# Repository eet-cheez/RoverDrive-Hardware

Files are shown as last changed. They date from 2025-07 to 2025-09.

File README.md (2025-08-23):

# RoverDrive-Hardware
A custom PCB for a robot powered by an esp32 microcontroller that has pins to control 4 servos plus one for sub-micro servo at 3.3v (in case it burns out at 5v). It also can support multiple other devices like LEDs or sensors and has an IMU to know its direction.





### Why am I doing this?
Last year, I built a robot that was controlled by connecting to an app. The problem is that the inside was a mess of wires and modules floating around, so it was a pain to fix and improve. I decided a PCB could fit more features while also being much easier to assemble and access.

## Details
- The microcontroller is an ESP32-S3-mini-1. I only really chose it because it seemed compact, but there are probably much better options. 
- For the IMU, it uses a BNO055, which does all of the calculations internally to find its orientation. Might be a bit overkill, but I want to make sure it works properly.
- The board uses a basic ams1117-3.3 to to power all of the 3.3v devices.
- Power is supplied to the board via a 1s lipo battery, which gets boosted to 5v by a mt3608 regulator.
- PCB designed in KiCad.
### Schematic: 

### PCB: 


#### CAD:
This is that the robot looks like with a model of the PCB (in TinkerCad):
 


The robot chassis needed to be changed to fit the PCB. Files have been attached if needed.

## BOM
| Item | Description | Quantity | Cost |
|---|---|---|---|
|ESP32-S3-MINI-1-N8|	the microcontroller	|1	|$6.15 |
|NFM18PC104R1E3D|	100nf capacitor	|13	|$1.69|
|PTS647SN50SMTR2 LFS|	reset and boot buttons|	2	|$0.46|
|GRM188C81A226ME01D|	22uf ceramic capacitor|	3	|$0.87|
|TAJA226K010RNJ|	22uf tantalum capacitor. for ams1117-3.3	|2|$0.70|
|SS34| schottky diode	|1|$0.52|
|SRP7028AA-220M|	22uh inductor	for 5v regulator|1|$1.11|
|C1608X7T1A106M080AC|	10uf ceramic capacitor	|3|	$0.69|
|06031A220FAT2A|	22pf ceramic capacitor for gyro|3	|$1.32|
|CRCW060310K0FKEI|	10k resistor	|7	|$1.05|
|CRCW06035K10FKEC|	5.1k resistor	|3	|$0.36|
|RNCE0603BTE1K00|	1k resistor	|2|$0.42|
|ERJ-3RBD7501V|	7.5k resistor	|2|$0.30|
|ABS07-32.768KHZ-7-T|	32.768 kHz crystal for gyro|1|$0.82|
|BNO055|	9 axis IMU	|1|$12.34|
|USB4105-GF-A	|USB c receptacle, 16 contact|1|$0.78|
|MT3608|	boost converter. used to increase battery voltage to 5v (already have)|	1	|$0|
|AMS1117-3.3|	3.3v voltage regulator	|1	|$0|
|2.54mm pin headers	|for servos	|5| $0|
|Molex picoblade connector|fits with the battery, probably|1|$0|
|JST Connectors (2-pin, 3-pin, 4-pin)|Probably JST XH|3|$0|
|PCB|from JLCPCB|1|$41.71 **(See below for price explanation)***|
**Total:			$71.29**

Sheet with part links: https://docs.google.com/spreadsheets/d/1vR1n98YzZK8dJmbvGAbjTAVUf36cDbNLpNew4ql-z88/edit?usp=sharing

### * PCB Price Explanation
I'm exhibiting the full Roverdrive project at Open Sauce this year and did not have much time to create the hardware (need to finish by the 19th, difficult with Undercity taking up time). In order to get the PCB on time, I had to pay way more for shipping and couldn't spend much time optimizing the cost. I've already bought all of the parts, and I understand if Hack Club doesn't want to reimburse the full cost. If needed, I would gladly take a smaller, more reasonable reimbursement.

### Finished Project




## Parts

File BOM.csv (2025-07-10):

Item | Description | Amount | Total Cost
ESP32-S3-MINI-1-N8 |  | 1 | $6.15
NFM18PC104R1E3D | 100nf capacitor | 13 | $1.69
PTS647SN50SMTR2 LFS | reset and boot buttons | 2 | $0.46
GRM188C81A226ME01D | 22uf ceramic capacitor | 3 | $0.87
TAJA226K010RNJ | 22uf tantalum capacitor. for ams1117-3.3 | 2 | $0.70
SS34 | ss34 schottky diode | 1 | $0.52
SRP7028AA-220M | 22uh inductor | 1 | $1.11
C1608X7T1A106M080AC | 10uf ceramic capacitor | 3 | $0.69
06031A220FAT2A | 22pf ceramic capacitor | 3 | $1.32
CRCW060310K0FKEI | 10k resistor | 7 | $1.05
CRCW06035K10FKEC | 5.1k resistor | 3 | $0.36
RNCE0603BTE1K00 | 1k resistor | 2 | $0.42
ERJ-3RBD7501V | 7.5k resistor | 2 | $0.30
ABS07-32.768KHZ-7-T | 32.768 kHz 3.2 mm x 1.5 mm crystal | 1 | $0.82
BNO055 | 9 axis IMU | 1 | $12.34
USB4105-GF-A | USB c receptacle, 16 contact | 1 | $0.78
MT3608 | boost converter. used to increase battery voltage to 5v (already have) | 1 | $0
AMS1117-3.3 | 3.3v voltage regulator (already have) | 1 | $0
2.54mm pin headers | for servos (already have) | 5 | $0
Molex picoblade connector | fits with the battery, probably (already have) | 1 | $0
JST Connectors (2-pin, 3-pin, 4-pin) | No specific type, just any that fit on the board. (already have) | 3 | $0
PCB (x5) + shipping + 1 day | from JLCPCB, see readme for explanation | 1 | $41.71
Total: |  |  | $71.29
Sheet with Links: |  |  | https://docs.google.com/spreadsheets/d/1vR1n98YzZK8dJmbvGAbjTAVUf36cDbNLpNew4ql-z88/edit?usp=sharing

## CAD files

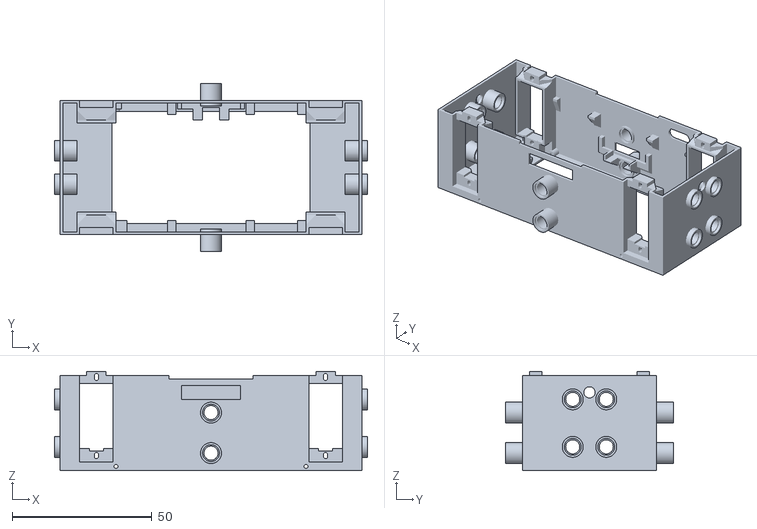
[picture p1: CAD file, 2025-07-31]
CAD/Roverdrive_Chassis.stl
112.0 x 60.0 x 35.5

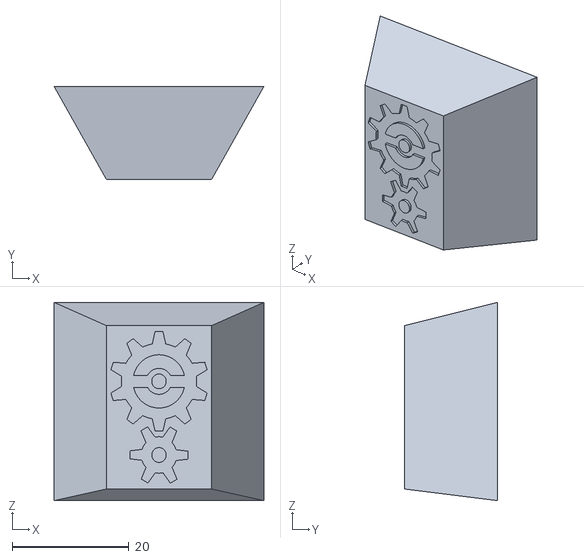
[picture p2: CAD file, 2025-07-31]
CAD/Roverdrive_Side.stl
36.0 x 16.0 x 34.0

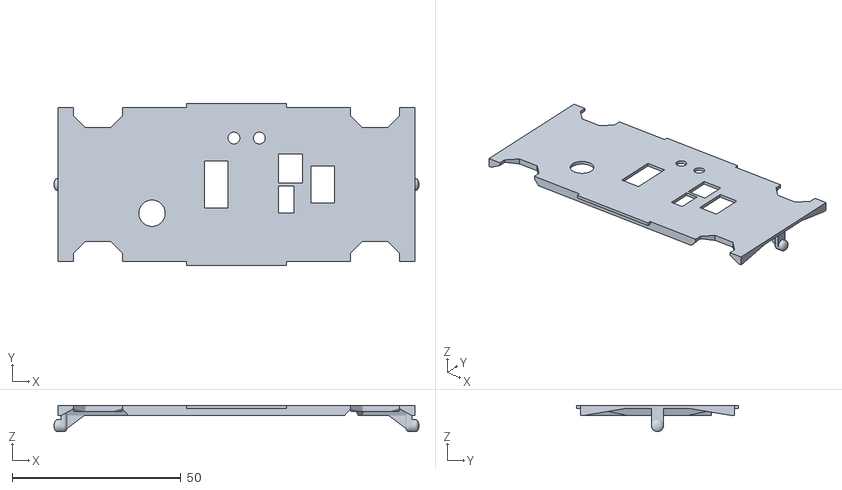
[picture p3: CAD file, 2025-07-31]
CAD/Roverdrive_Lid.stl
108.0 x 48.0 x 7.80

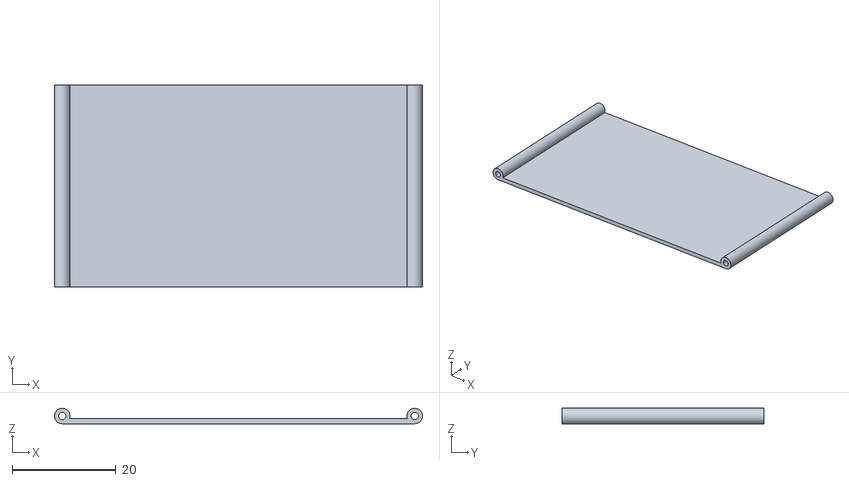
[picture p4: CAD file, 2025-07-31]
CAD/Roverdrive_BottomDoor.stl
71.0 x 39.0 x 3.00

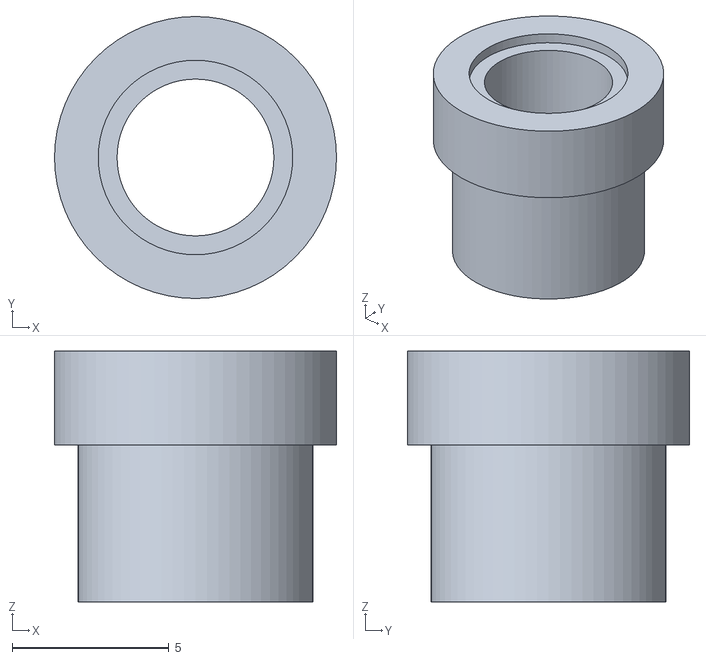
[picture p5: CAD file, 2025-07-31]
CAD/LidHoleConnection.stl
9.00 x 9.00 x 8.00

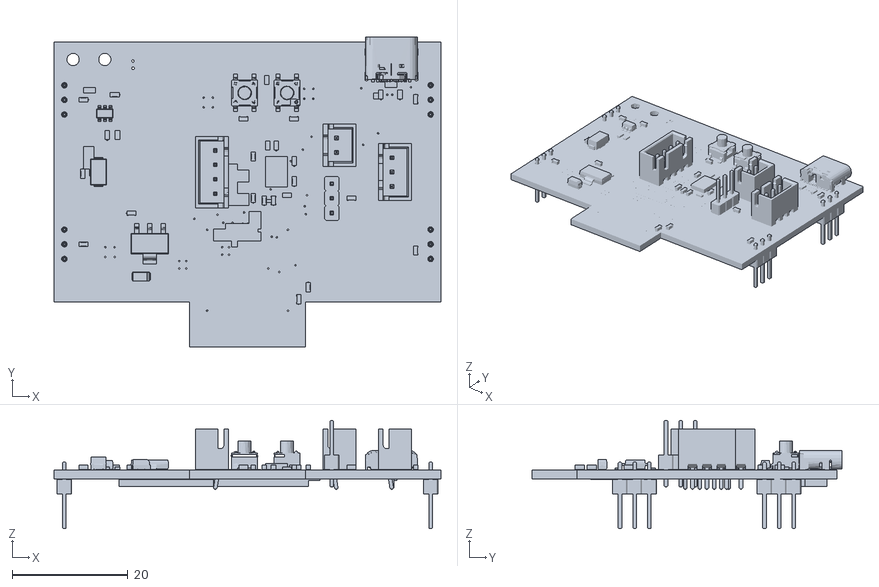
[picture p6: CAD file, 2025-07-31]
CAD/Roverdrive_PCB.stl
67.0 x 53.7 x 18.8

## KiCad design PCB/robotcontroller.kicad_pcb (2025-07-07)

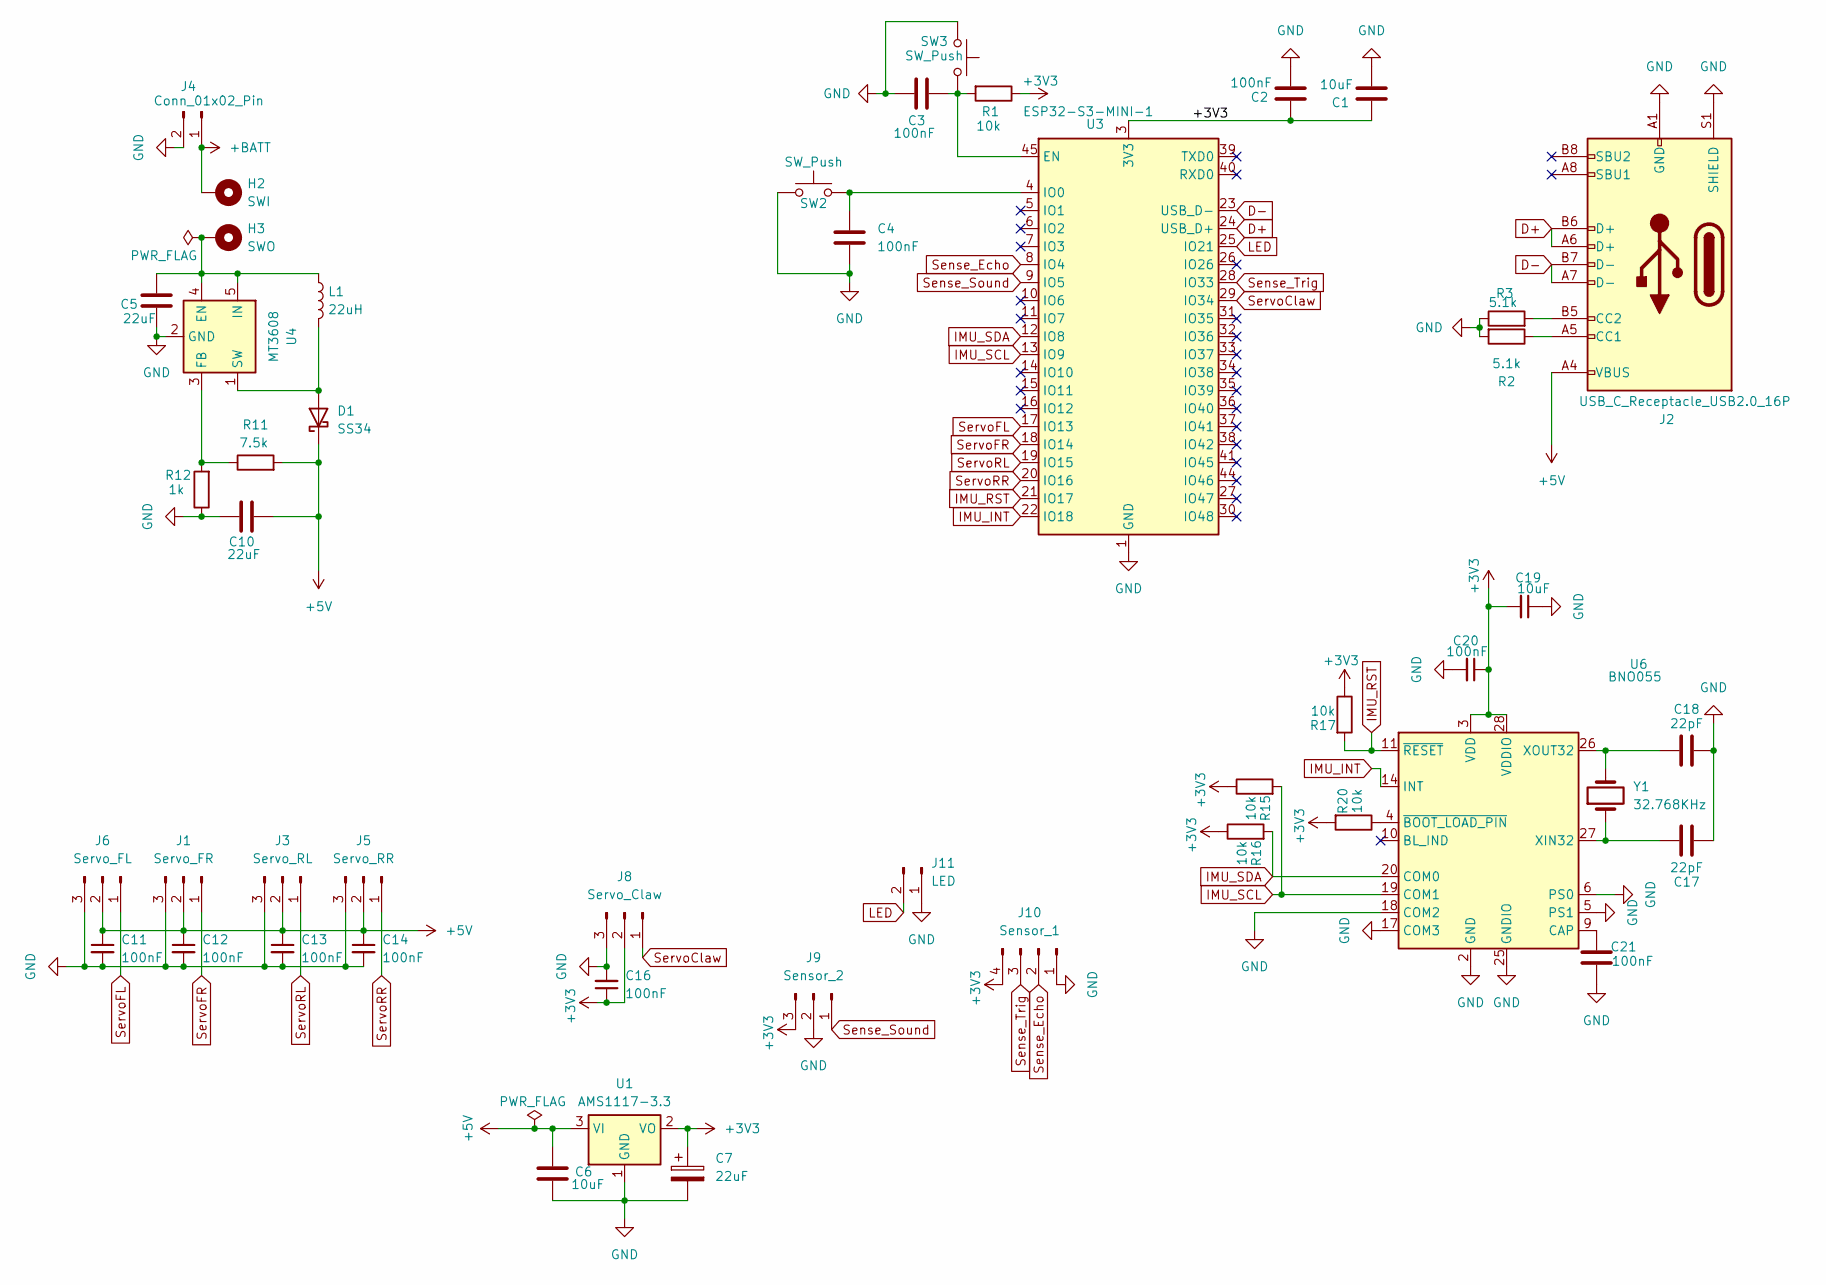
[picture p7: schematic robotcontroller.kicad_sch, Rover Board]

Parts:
C1, C6, C19: 10uF; C_0603_1608Metric
C2, C3, C4, C11, C12, C13, C14, C16, C20, C21: 100nF; C_0603_1608Metric
C5, C10: 22uF; C_0603_1608Metric
C7: 22uF; CP_EIA-3216-18_Kemet-A
C17, C18: 22pF; C_0603_1608Metric
D1: SS34; D_SMA
H2: SWI; SolderWire-1.5sqmm_1x01_D1.7mm_OD3mm
H3: SWO; SolderWire-1.5sqmm_1x01_D1.7mm_OD3mm
J1: Servo_FR; PinHeader_1x03_P2.54mm_Vertical
J2: USB_C_Receptacle_USB2.0_16P; USB_C_Receptacle_GCT_USB4105-xx-A_16P_TopMnt_Horizontal
J3: Servo_RL; PinHeader_1x03_P2.54mm_Vertical
J4: Conn_01x02_Pin; Molex_PicoBlade_53048-0210_1x02_P1.25mm_Horizontal
J5: Servo_RR; PinHeader_1x03_P2.54mm_Vertical
J6: Servo_FL; PinHeader_1x03_P2.54mm_Vertical
J8: Servo_Claw; PinHeader_1x03_P2.54mm_Vertical
J9: Sensor_2; JST_XH_B3B-XH-A_1x03_P2.50mm_Vertical
J10: Sensor_1; JST_XH_B4B-XH-A_1x04_P2.50mm_Vertical
J11: LED; JST_XH_B2B-XH-A_1x02_P2.50mm_Vertical
L1: 22uH; L_Bourns_SRP7028A_7.3x6.6mm
R1, R15, R16, R17, R20: 10k; R_0603_1608Metric
R2, R3: 5.1k; R_0603_1608Metric
R11: 7.5k; R_0603_1608Metric
R12: 1k; R_0603_1608Metric
SW2, SW3: SW_Push; SW_SPST_PTS647_Sx50
U1: AMS1117-3.3; SOT-223-3_TabPin2
U3: ESP32-S3-MINI-1; ESP32-S2-MINI-1
U4: MT3608; SOT-23-6
U6: BNO055; LGA-28_5.2x3.8mm_P0.5mm
Y1: 32.768KHz; XTAL_ABS07-32.768KHZ-7-T

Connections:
+3V3: C1.1, C2.1, C7.1, C16.1, C19.2, C20.1, J8.2, J9.3, J10.4, R1.1, R15.1, R16.1, R17.1, R20.2, U1.2 (VO), U3.3 (3V3), U6.3 (VDD), U6.28 (VDDIO)
+5V: C6.2, C10.2, C11.1, C12.1, C13.1, C14.1, D1.1 (K), J1.2, J2.A4 (VBUS), J2.A9 (VBUS), J2.B4 (VBUS), J2.B9 (VBUS), J3.2, J5.2, J6.2, R11.2, U1.3 (VI)
+BATT: H2.1, J4.1
D+: J2.A6 (D+), J2.B6 (D+), U3.24 (USB_D+)
D-: J2.A7 (D-), J2.B7 (D-), U3.23 (USB_D-)
GND: C1.2, C2.2, C3.2, C4.2, C5.1, C6.1, C7.2, C10.1, C11.2, C12.2, C13.2, C14.2, C16.2, C17.1, C18.2, C19.1, C20.2, C21.2, J1.3, J2.A1 (GND), J2.A12 (GND), J2.B1 (GND), J2.B12 (GND), J2.S1 (SHIELD), J3.3, J4.2, J5.3, J6.3, J8.3, J9.2, J10.1, J11.1, R2.2, R3.1, R12.1, SW2.1, SW3.1, U1.1 (GND), U3.1 (GND), U3.2 (GND), U3.42 (GND), U3.43 (GND), U3.46 (GND), U3.47 (GND), U3.48 (GND), U3.49 (GND), U3.50 (GND), U3.51 (GND), U3.52 (GND), U3.53 (GND), U3.54 (GND), U3.55 (GND), U3.56 (GND), U3.57 (GND), U3.58 (GND), U3.59 (GND), U3.60 (GND), U3.61 (GND), U3.62 (GND), U3.63 (GND), U3.64 (GND), U3.65 (GND), U4.2 (GND), U6.2 (GND), U6.5 (PS1), U6.6 (PS0), U6.17 (COM3), U6.18 (COM2), U6.25 (GNDIO)
IMU_INT: U3.22 (IO18), U6.14 (INT)
IMU_RST: R17.2, U3.21 (IO17), U6.11 (~RESET)
IMU_SCL: R15.2, U3.13 (IO9), U6.19 (COM1)
IMU_SDA: R16.2, U3.12 (IO8), U6.20 (COM0)
LED: J11.2, U3.25 (IO21)
unnamed: D1.2 (A), L1.2, U4.1 (SW)
unnamed: J2.A5 (CC1), R2.1
unnamed: J2.B5 (CC2), R3.2
unnamed: C3.1, R1.2, SW3.2, U3.45 (EN)
unnamed: C4.1, SW2.2, U3.4 (IO0)
unnamed: C5.2, H3.1, L1.1, U4.4 (EN), U4.5 (IN)
unnamed: R11.1, R12.2, U4.3 (FB)
unnamed: C21.1, U6.9 (CAP)
unnamed: C17.2, U6.27 (XIN32), Y1.1
unnamed: C18.1, U6.26 (XOUT32), Y1.2
unnamed: R20.1, U6.4 (~BOOT_LOAD_PIN)
Sense_Echo: J10.2, U3.8 (IO4)
Sense_Sound: J9.1, U3.9 (IO5)
Sense_Trig: J10.3, U3.28 (IO33)
ServoClaw: J8.1, U3.29 (IO34)
ServoFL: J6.1, U3.17 (IO13)
ServoFR: J1.1, U3.18 (IO14)
ServoRL: J3.1, U3.19 (IO15)
ServoRR: J5.1, U3.20 (IO16)

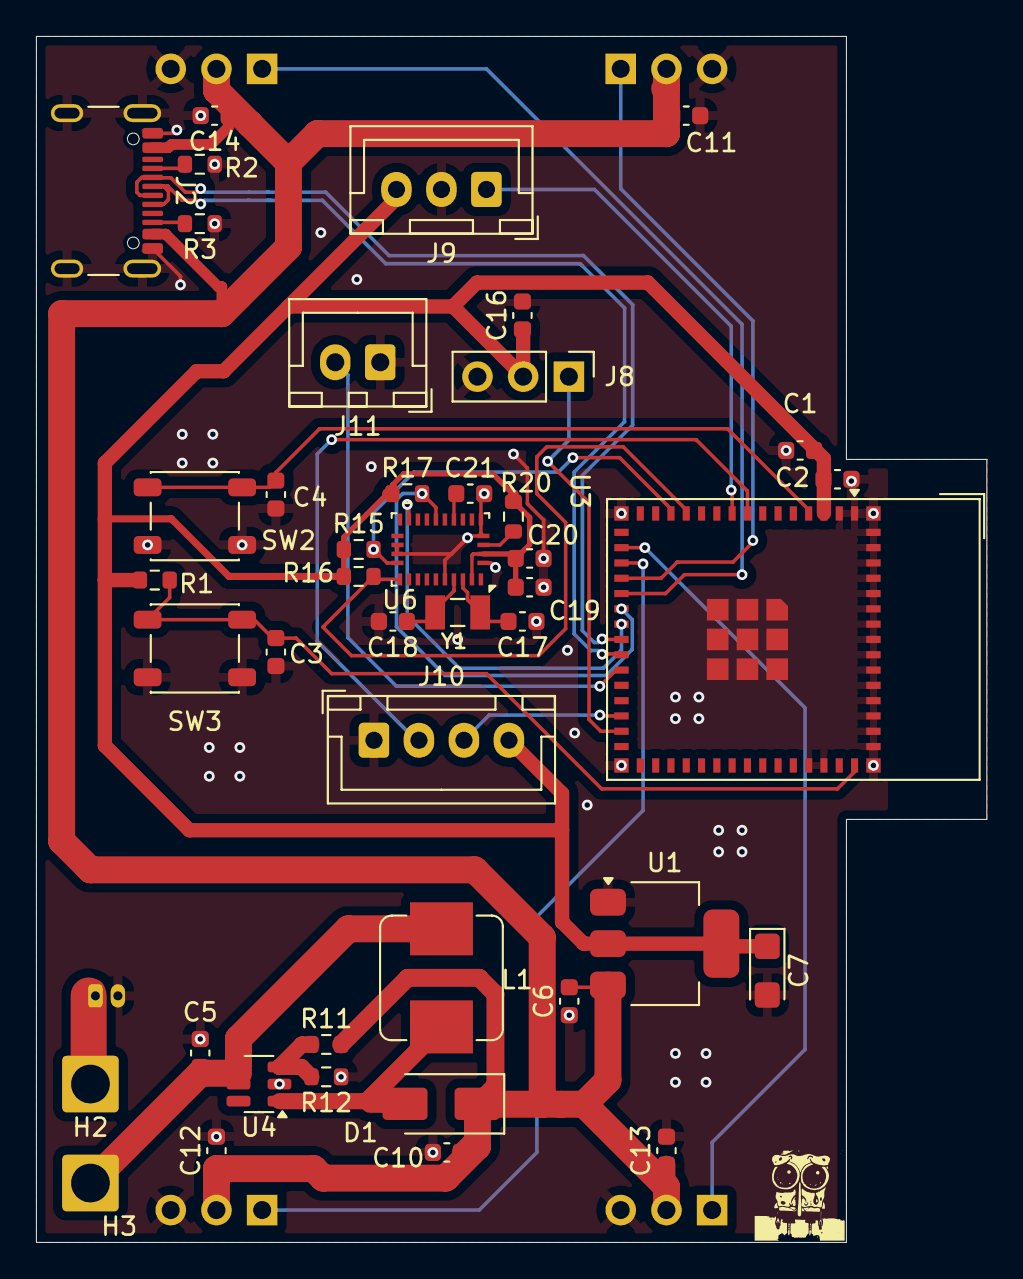
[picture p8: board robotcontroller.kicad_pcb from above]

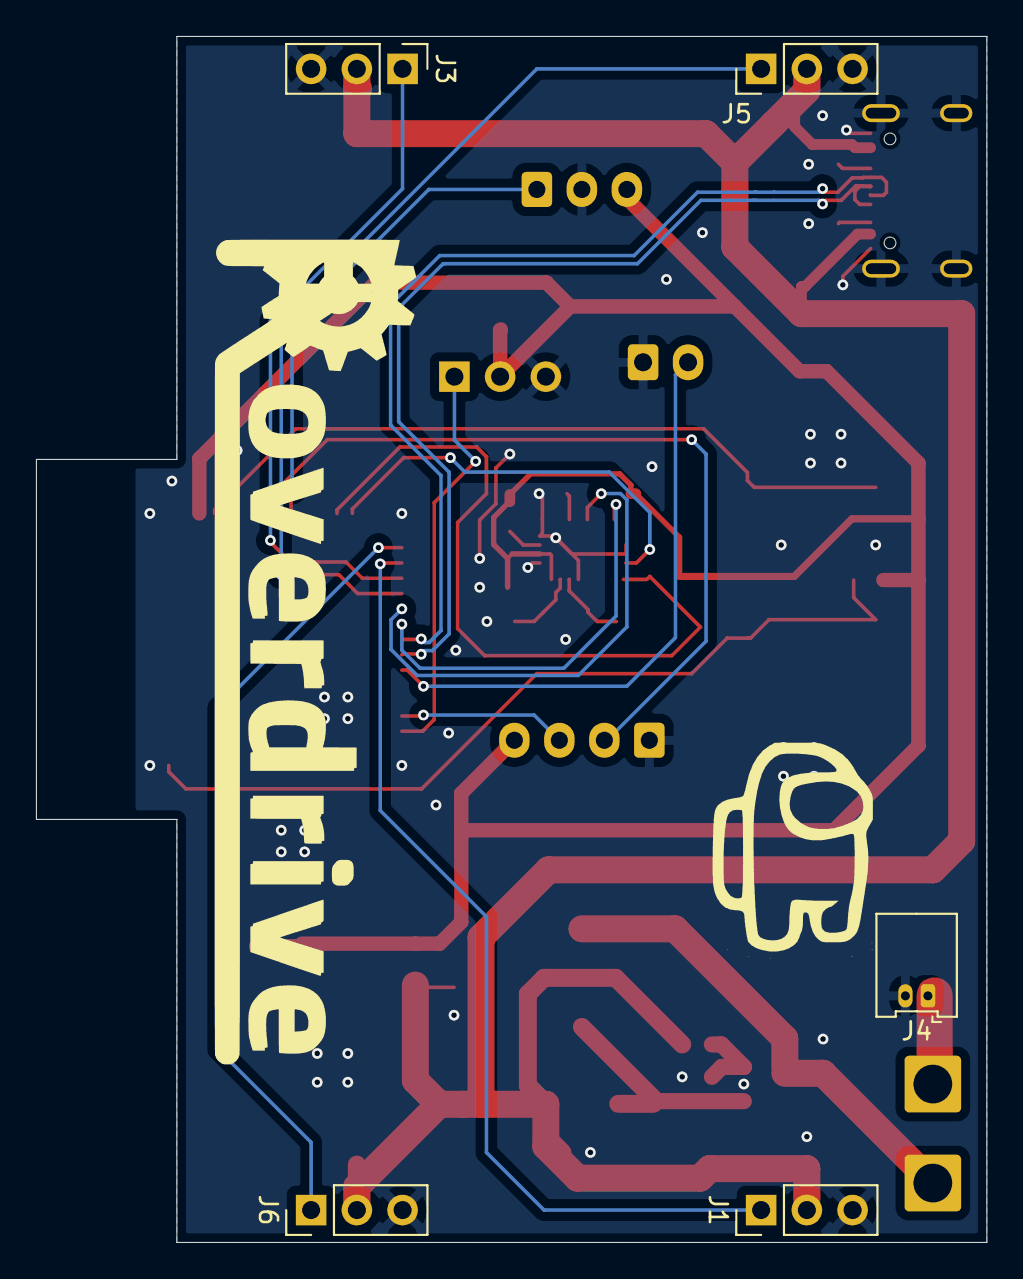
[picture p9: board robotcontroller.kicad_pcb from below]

Board: 2 copper layers, 52.8 x 67.0 mm, 48 parts (5 on the bottom side), 30 nets.

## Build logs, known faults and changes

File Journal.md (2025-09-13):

---
title: "RoverDrive Hardware"
author: "Dylan Itoh"
description: "A PCB for a robot"
created at: "2025-06-24"
---
### Total time: about 27 hours
# Journal

## Day 1 - 6/24
I mostly spent this time planning what features the control board needs. It must be able to connect to to an app, have many pins for sensors, leds, and servos, and possibly add new stuff like gyro and battery charging.
I think I might use an esp32 s3 mini module.
## Time Spent: 1 hour

## Day 2 - 6/25
Started on the schematic for the microcontroller part. I have never really done this before so I watched some tutorials.

I added reset and boot button circuits, some caps on its 3.3v input, and a usb c connector.



Because the power is on 5v, i needed to add a voltage regulator. AMS1117-3.3 is very common, so i used it.

## Time Spent: 3 hours

## Day 3 - 6/26
now, I need to do the battery charging. I normally use a 2 cell lithium battery, but I'll switch to a single cell lipo because the circuit is probably simpler. Then I made the circuit by looking at a video and the datasheets of each part.


It uses a separate usbc connector for charging. has tp4056 as the carging IC, a fs312f for protection, and an mt3608 for boosting it to 5v. I also added two empty wire holes for a switch

## Time Spent:  5 hours

## Day 4 - 6/28
Started doing the gyro/accelerometer for the robot. The robot will need to know the direction it is facing. some options are the mpu9250 and icm 20948, but you need to do extra complex stuff to calculate its orientation. 
While researching these, I saw the bno055 sensor which is very accurate, but there arent very many pictures of schematics I could find for reference. I have been looking at the schematic in its datasheet and also the schematic of the Adafruit breakout board

## Time Spent:  4 hours

## Day 5 - 6/29
Finished the imu schematic:



All thats left is to add the connectors for sensors and servos and an led. 

I added 6 3-pin connectors (one for each 5v wheel servo, one for a tiny grabber arm servo, and another for a some extra 3.3v sensor), then I added a 4-pin connector for a distance sensor and a 2-pin connector for a controllable LED. 
It looks like this:


## Time Spent:  2 hours

## Day 6 - 6/30
The schematic is done, now I'm picking the footprints.

I decided to remove the entire charging circuit because it's too complex and is just unnecessary. I realized I usually just replace the dead battery with a charged one because I need to use it continuously.
## Time Spent:  3 hours

## Day 7 - 7/1
I need to make the PCB now. It must fit within a space of 45mmx67mm and should have all connectors (except for wheel and battery) inside the orange area, like shown: 


I placed all of the parts on the board. All the power components are all at the bottom. The esp32 sticks out of the side. I also tried to put all of the gyro parts in the center of the board so it is more accurate. The wheel servo headers and battery connectors are on the other side. It looks like this: 



I learned how to add ground planes to the pcb, so I added it to both sides.

I started the 5v power traces at the battery and made it super thick, around 1mm to 1.5mm.

Then, I did the 3.3v power traces, which goes from the regulator to the ESP module and all of the sensors. Both traces had to be routed along the side of the board because there wasnt much space.

I finally connected all of the signal pins. They had to go on both sides and needed vias. I also noticed that the ground plane got split up in many areas, so vias were needed to connect it to the other side
## Time Spent:  5 hours

## Day 8 - 7/2
The PCB is almost done, so I ran a design rules checker. It told me a bunch of the gnd pads werent right, so I added vias on them. Also, a bunch of wires were not connected yet, so I fixed them.

I moved all of the silkscreen stuff in better places to get rid of most of the warnings.

I learned how to add images on the silkscreen, so I added a few.

Its finished



## Time Spent:  1 hour

## Day 9 - 7/23
multiple changes had to be made to the CAD model to make the PCB fit well inside it:
- all of the old inside stuff was removed
- a hole was added to the side of the base for the ESP to stick through
- supports added to the edge of the base inside for the board to rest on
- top lid of the body had to be modified to prevent it from colliding with components on the PCB
- holes added in the top lid for connectors and the reset+boot buttons
- side connector holes moved around to make space for switch
- hole and support added for a power switch on the side of the base
- door added to the bottom of the base for easy battery access

Before:



After: 



## Time Spent:  3 hours

## Assembly

## 7/18-19

I got all of the components and the pcb: 



So all that's left to do is solder everything. First, I attached all of the capacitors, then resistors, then all of the power supply components and battery plug. I wanted to test if it powered up, and I ran into a big problem. After plugging the battery in, it heated up and the regulator components started smoking. Using a multimeter, I found that there was a short between 5v and gnd. I decided it was best to keep removing components until it stopped showing continuity. It turned out to all be caused by the 100nf capacitors, which for some reason had continuity between both ends. Maybe I got the wrong type. I decided to move on without battery power and focus on the actual microcontroller. I used a heat gun and solder paste to attach the IMU, which was kind of hard and took a few tries. Soldering the ESP was almost impossible, but I attached it by heating from the bottom. I soldered the usb receptacle last, and it got kind of melty. When plugging it in, it got power, but would not show up as a device       

## 7/28
I continued working on the pcb.

I assumed it was the bad soldering of the ESP that caused the problem. Or maybe I cooked the ESP after it being under the heat gun for so long. I unsoldered the module from the board and instead attached it using many thin wires. It might not look nice, but it should work.
After powering it on, It did not work. still the exact same as before.

## 8/1
I came up with another idea that it might be the USB port that was not soldered well. I noticed that the pads of the receptacle were all lifted up, except for the power ones, and were also super bent up. I replaced it with a port desoldered from a different board and made sure to press it down while soldering it on.

I probed around again with a multimeter to see if there were any issues. The data lines were connected to the USB, and were not connected to each other. After plugging it in, it still did not show as a device. I thought I might need to uploed firmware to activate it somehow, but I do not know how.
## 8/2
I started messing with the board again with a multimeter, and discovered that the ESP module wasn't even recieving power. The problem was really just the vcc wire accidentally being soldered to gnd. After fixing this one thing, the board actually worked and connected to the computer. It often disconnected though, and I assumed it was still the usb connector not soldered well. I pressed it to the board while heating it with a heat gun, and the issue dissapeared when plugging it in.



The board looks very burnt, but it atleast works.
Next, I made a test setup by wiring the motors and battery to the pcb. This is what it looked like:



All of the robot parts finished printing and I started putting them together. The chassis neeeded a switch installed and some parts had to be assembled by melting them together. The battery door could be attached with very thin (about 1mm diameter) pins. I used servo screws but I could have also used paperclips.



I installed the main components like servos, battery, pcb, into the chassis and wired them together again. The front wheels were replaced with omnidirectional wheels from an older version of the robot to make turning easier.
